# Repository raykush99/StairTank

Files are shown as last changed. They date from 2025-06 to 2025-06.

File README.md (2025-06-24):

**Stair Tank**      
Simply put, my project is a tank that can climb stairs. It is a RC car that uses treads to move instead of wheels. But to add on that, it had a special function that allows it to go up and down stairs. It also has a camera that can broadcast a live feed back to a device. The tank is controlled using the "wasd" keys on a computer.         

**Why a tank**         
I choose to build a tank since I have always wanted to make a remote control vehicle that can go anywhere. I always dreamed of being able to sit in any room and drive a car around the house, using a camera to see where it is. But I always face a boundry, since most RC cars are limited to being on one floor. Due to this, I decided to make something that can go up and down stairs, giving it almost limitless reach. From this also came the idea of being anywhere in the house, and being able to call the tank to come to your position. Or sitting in the basement and sending a box upsatirs on the car without moving muscle. This is what inspired me to make a RC car that can go anywhere, even up stairs.       
     
       
     

**BOM**      

|Item	|Unit Price|	Quantity|	Total Price|	Link|
| --- | -----|---|---|-----|
|Tank Treads	|12.8|	3|	38.4|	https://www.amazon.com/gp/product/B0BKFQPS5T/ref=ox_sc_act_title_10?smid=A3DNF7PMWIJNTG&psc=1|
|Tread Grip|	2.36	|3|	7.08	|https://www.amazon.com/gp/product/B0BHQKYL83/ref=ox_sc_act_title_1?smid=A2OG7GOMLN7OOH&th=1|
|DC Motor	|15.99	|2	|31.98|	https://www.amazon.com/gp/product/B09SZ3GC13/ref=ox_sc_act_title_9?smid=AMXT7HV26EJPE&th=1|
|Motor Driver|	6.98	|1	|6.98|	https://www.amazon.com/gp/product/B0DPPWFZ1C/ref=ox_sc_act_title_7?smid=A19I4QHRSJAHJQ&th=1|
|Servo Motor|	9.99|	1	|9.99	|https://www.amazon.com/gp/product/B09BZ5955Z/ref=ox_sc_act_title_6?smid=A19FRW2DHVT2CC&th=1|
|Battery	|15.99|	1	|15.99|	https://www.amazon.com/gp/product/B0C243MXMQ/ref=ox_sc_act_title_8?smid=A3FKMD6P089KQA&th=1|
|Switch	|5.29|	1	|5.29	|https://www.amazon.com/Rocker-Switch%EF%BC%8C6Pcs-Latching-Pre-Wired-KCD1-X-Y/dp/B07L9JWVVR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 303622651e1e&pf_rd_p=751acc83-5c05-42d0-a15e-303622651e1e&pf_rd_r=546HWN4ZDGJN150SFFDJ&pd_rd_wg=p7Kxs&pd_rd_r=c3ec9eda-920d-4ffe-a6fc-3ae20d09d0dd&pd_rd_i=B07L9JWVVR&psc=1|
|Voltage Stepdown|	8.99|	1	|8.99|	https://www.amazon.com/gp/product/B09DGDQ48H/ref=ox_sc_act_title_2?smid=A25NZ3OT6I61PQ&th=1|
|Esp32 microcontroller with camera	|14.99	|1	|14.99	|https://www.amazon.com/gp/product/B0F4DKTBR9/ref=ox_sc_act_title_5?smid=A23ZQFJGQ73FV0&th=1|
|ABS 1/8"	|35.99|	1	|35.99	|https://www.amazon.com/gp/product/B0CLVQV2RW/ref=ox_sc_act_title_4?smid=A14NQTB8LBA47J&th=1|
|ABS 0.06"	|17.99	|1	|17.99	|https://www.amazon.com/gp/product/B0B429DZ7H/ref=ox_sc_act_title_3?th=1|
|16 awg wire|	7.99|	1	|7.99	|https://www.amazon.com/Voltage-Automotive-Primary-Security-Electrical/dp/B0CZ73SQP8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|
|electrical tape|	3.59	|1|	3.59|	https://www.amazon.com/Wapodeai-Electrical-Temperature-Resistance-Waterproof/dp/B07ZWC2VLX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|
|Gyro sensor|	0	|1|	0	|own|
|Total Price		|	205.25|

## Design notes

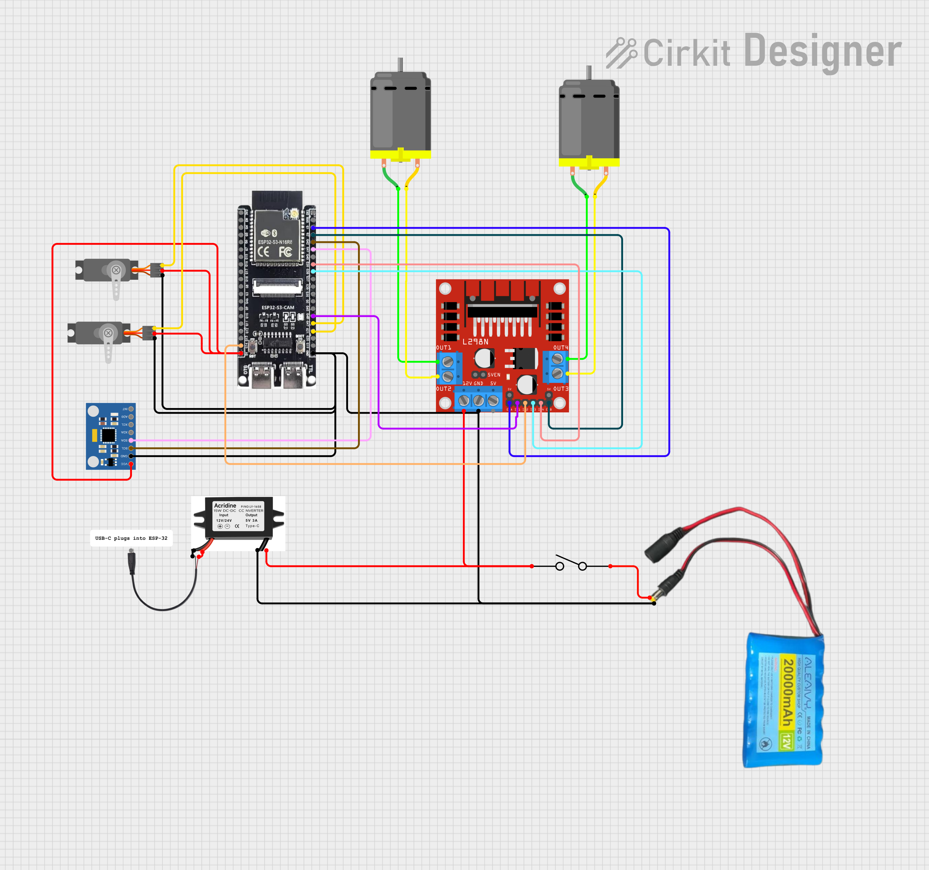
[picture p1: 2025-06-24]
circuit.png

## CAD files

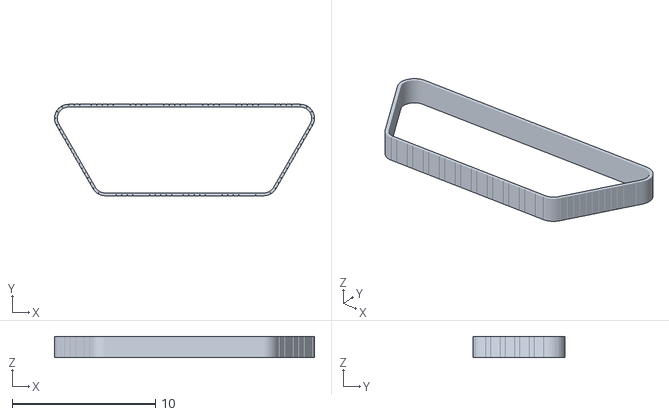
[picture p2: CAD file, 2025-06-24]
CAD/Tread Main.stl
18.2 x 6.40 x 1.50

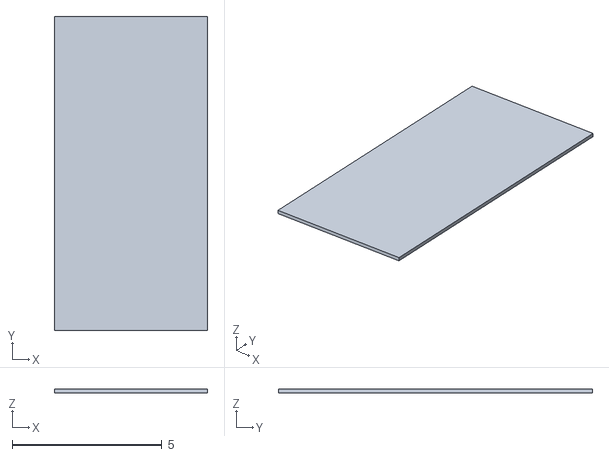
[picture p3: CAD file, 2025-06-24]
CAD/Back panel.stl
5.12 x 10.5 x 0.125

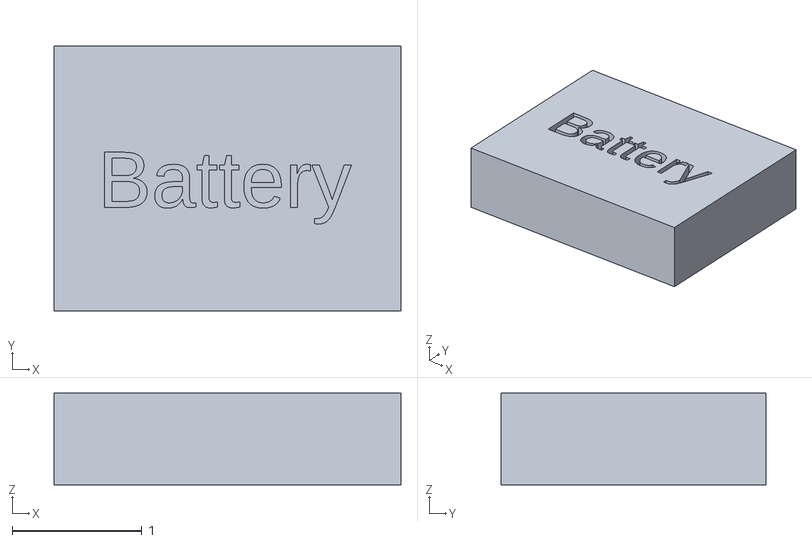
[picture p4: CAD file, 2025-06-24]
CAD/battery.stl
2.68 x 2.05 x 0.709

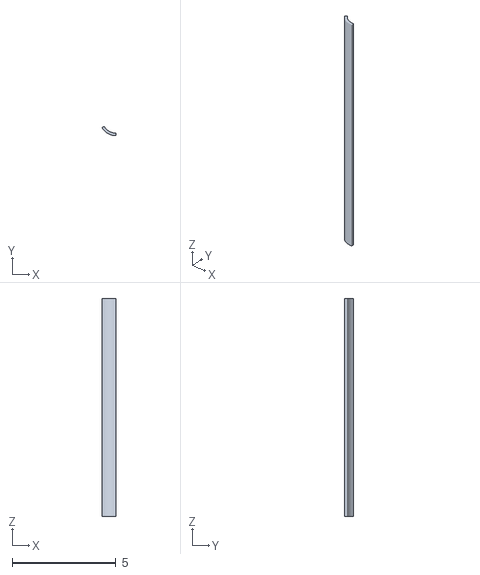
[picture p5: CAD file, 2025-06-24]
CAD/Bottom Back.stl
0.68 x 0.455 x 10.5

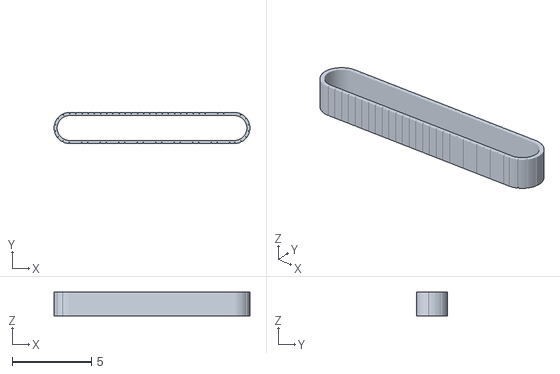
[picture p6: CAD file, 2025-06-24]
CAD/Tread Assist.stl
12.4 x 1.97 x 1.50

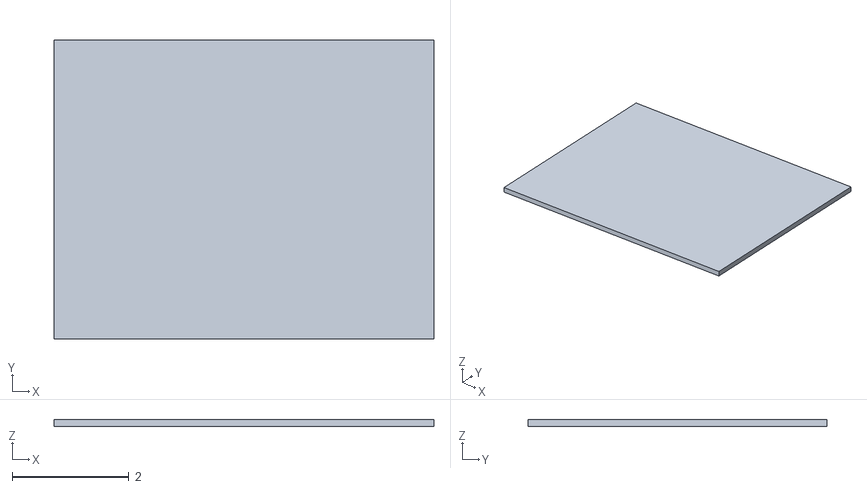
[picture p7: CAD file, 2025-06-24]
CAD/Front Panel.stl
6.50 x 5.12 x 0.125

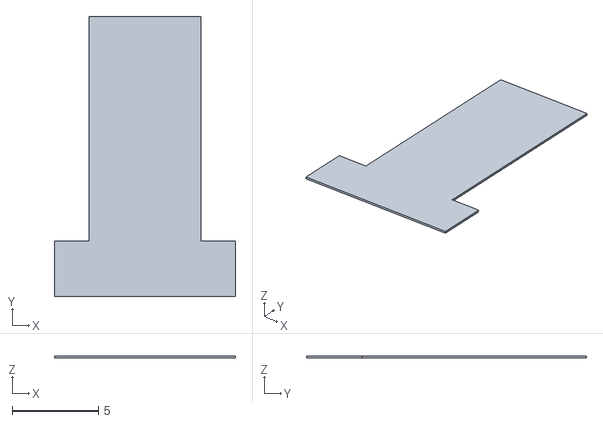
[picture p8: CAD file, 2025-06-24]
CAD/Top Panel.stl
10.5 x 16.2 x 0.125

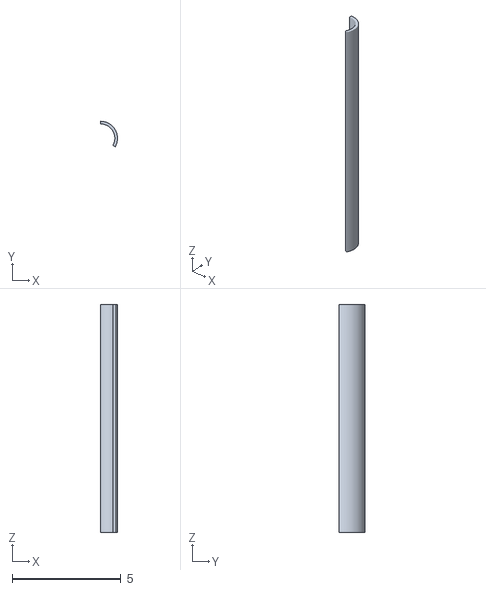
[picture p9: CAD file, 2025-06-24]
CAD/Top Back.stl
0.785 x 1.18 x 10.5

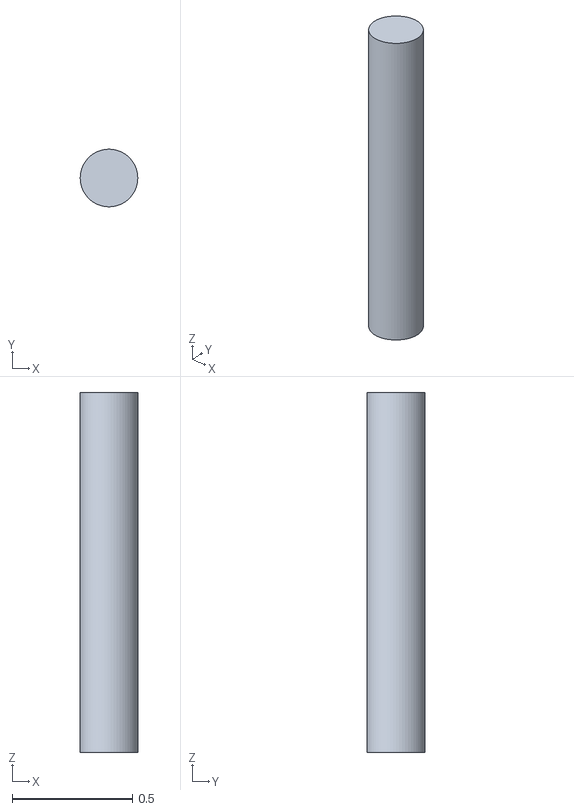
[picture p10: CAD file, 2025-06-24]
CAD/Small axle.stl
0.24 x 0.24 x 1.50

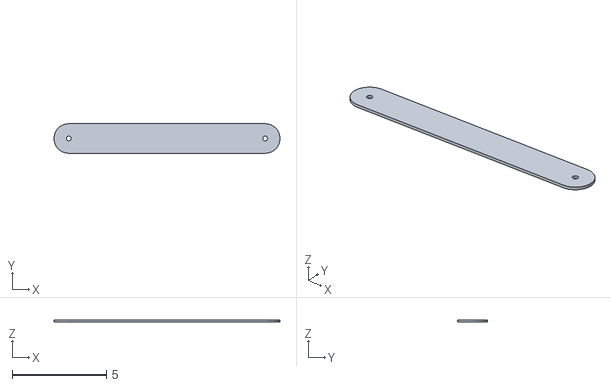
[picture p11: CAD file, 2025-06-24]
CAD/Assist Panels.stl
12.0 x 1.57 x 0.125

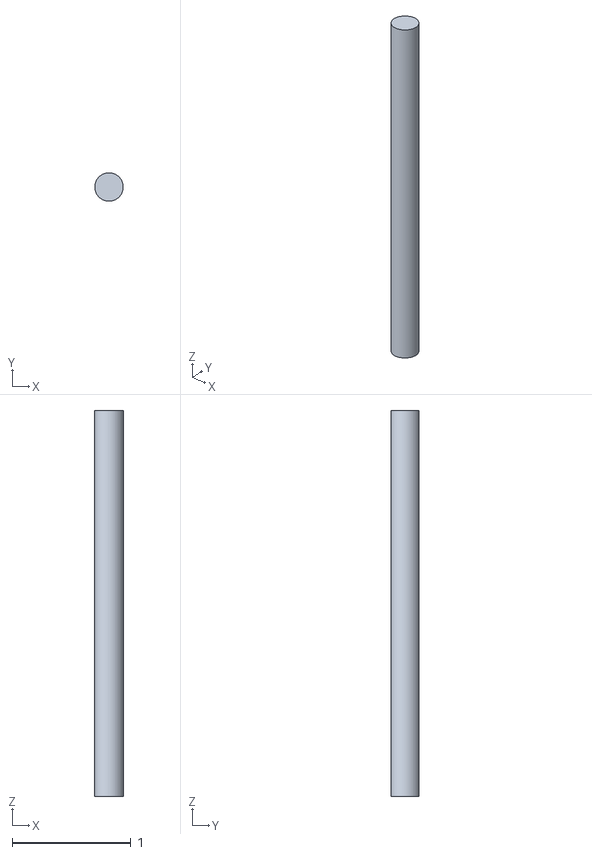
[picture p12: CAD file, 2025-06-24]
CAD/Large axle.stl
0.24 x 0.24 x 3.25

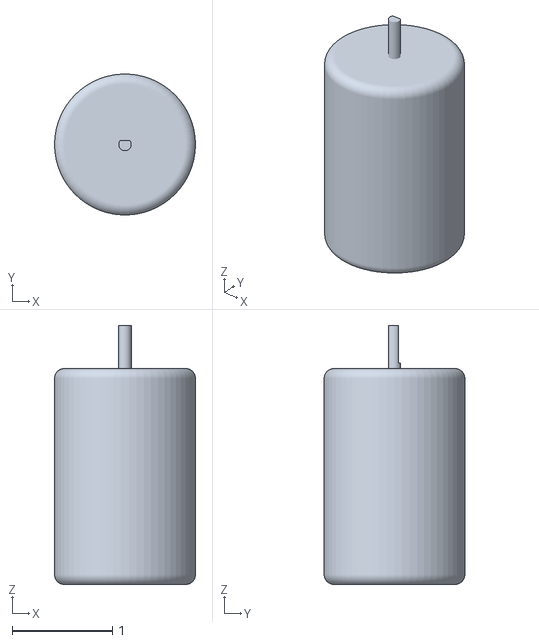
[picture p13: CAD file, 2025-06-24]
CAD/motor.stl
1.41 x 1.41 x 2.59

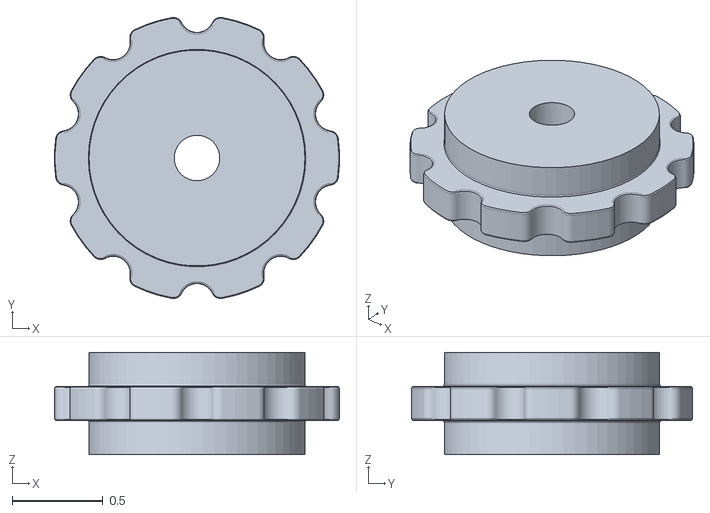
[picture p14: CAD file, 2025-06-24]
CAD/Tread Gear.stl
1.57 x 1.55 x 0.562

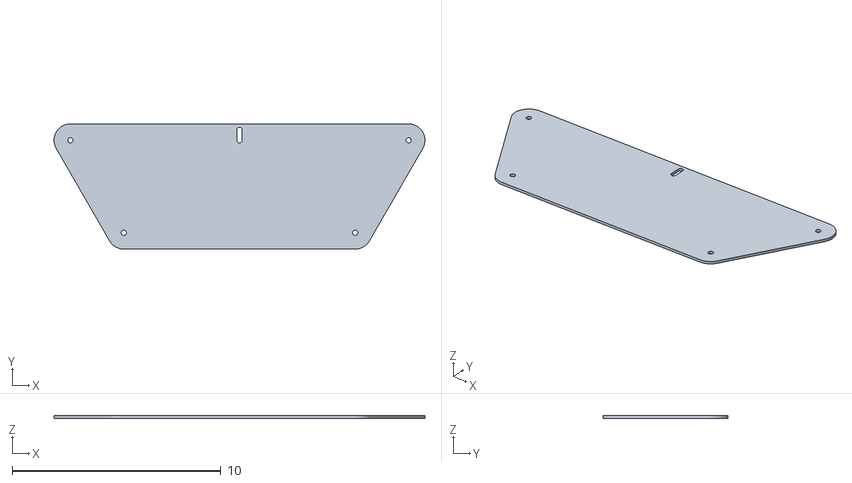
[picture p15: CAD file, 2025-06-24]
CAD/Side Walls.stl
17.8 x 6.00 x 0.125

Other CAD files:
CAD/Bottom Front.stl
CAD/Top Front.stl
CAD/Bottom Panel.stl
CAD/servo.stl

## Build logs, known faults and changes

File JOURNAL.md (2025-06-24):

---
title: "Stair Tank"
author: "Kush Ray"
description: "A tank style RC car with camera that is able to go up and down stairs"
created_at: "2025-06-14"
---
**Total time spent: 13**

**Day 1 June  13**       

Today I began my researching different methods of building a stair climbing robot. The main method I found was a modular robot in which each section could lift up one by one to climb stairs one at a time. I did not use this since I wanted to be able to place items on the top of my robot, and this would make that difficult. I wondered if there was a way the robot could directly go over the stairs, but that would require wheels bigger than 8 inches in raduis. I then had the idea of using tank treads. However, that would still need very long treads. Instead, I decided to make a way to expand the size of the treads, by including another set that can come out of the body of the robot. I used some spare LEGO pieces to make a quick prototype of the tread design, making sure it would work. After much trial and error, I found that including studs on the tracks helped it hold onto the stairs better. I also concluded that keeping a 45 degree angle was most effective in getting the treads to initially pull the robot up.    
             

**Time spent: 1.5 hours**

**Day 2 June 16**             
Today I began working on the CAD. I knew the tank had to be large to climb the stairs, so I decided to make it 18" x 12" x 12". I started making the panel that would hold the treads, and added fillets on the corners so the treads would be completly flush against the panel. I also added an extra hole in case the treads need to be tensioned. Next, I make a simple CAD of the wheel as well as making the axles. I did the same thing to make the panels for the expanding treads, and made panels to connect the two tread panels together to get a basic form of the tank. I assembled all the parts together to see how the second treads would flip out from the front. One hard part was making the curved panels since they had to be the right angle and radius to work. I managed to use the sketch of the tread panels as reference for the radius and angle to make the curves panels.            

      
      

**Time spent: 3 hours**

**Day 3 June 17**             
Today was mainly for finding the parts to build the tank. I decided to use lego treads, since they could be fit to any size, and I was able to add grip stubs on them to help climb the stairs. Doing some research, I also found that the L298N board was best for controlling the direction and speed of two motors. I also decied that a 35T motor would give the best torque and spped for the tank, and found a rechargable 12V battery to use. The last thing I thought of was how to flip the secondary treads. I decided on a servo motor since it would be best on keeping a 45 degree angle with the stairs. I also found strong servos to be able to lift the secondary treads.           

               
**Time spent: 1 hour**

**Day 4 June 19**            
Today I edited my cad to change the size based on parts I found and to add more detail. I started by adding detail to the gears. Then, I had to make the axles and space between the tread panels bigger, since the LEGO treads I found were bigger than I expected. After making this change, I had to fix my assembly, since the editing of the size caused some elements to become offset and merge. I also had to edit some dimensions of the panels to adjust for the large tread size. Finally, I added the treads to my design. This was the hardest and most time consuming part, since the treads werean irrugular shape. I wasn't able to animate the treads, but I was able to make a static design to simulate where they would go. I also added revolve mates and gear relations on the axle and gears to show how they will all move together.              

                                

**Time spent: 2.5 hours**

**Day 5 June 20**                
Today, I looked for the rest of the parts. Since I want a camera, I was planning on using the esp32-cam. However, this model does not have enough ports to be able to handle all the motors I need. After some searching, I found the esp32-S3-cam, a camera board with more gpio pins. I also spent some time seeing which gpio pins were usable and not taken up by the camera and other internal functions. Another problem I had was how to build the acutal tank. I though 3D printing, but the panels were too big. Instead, I decided to use polycarb or plastic. But since my design has curved parts, I eventually settled for ABS, since it is cheaper than polycarb, but also easier to bend into the curved shape I want. I spent time to plan out how I was going to cut each panel out, in order to have to buy the  least amount of material possible. I decided to use 1/8 inch for the main pieces, and 0.06 inch for the curved and smaller pieces.        

               
**Time spent: 1 hour**

**Day 5 June 20**               
My second work session on the 20th included me making the circuit diagram. I found a website that had many parts and allowed for an easy way to make visual diagrams. I started by importing in all the parts. I decided on not using a pcb, since most components were spread out and a pcb would be impractical. The cicurt included two servo motors, two dc motors, a motor driver, the esp32, the gyro sensor (to read the tilt of the tank on the stairs), a battery, a switch (to turn the power on and off), and a voltage stepdown. Halfway through wiring the power, I realized I didn't have a way to power the microcontroller. I wanted everything to have power using one battery, but the esp32 would fry with a 12V battery. I did research and found a voltage stepdown can convert the 12V to 5V. The model I found even had a usbc end to connect directly to the microcontroller to power it. Another problem was deciding which pins to use on the microcntroller. This is since some pins are connected to internal functions that may cause the pin not to work. I used the pin diagram given my the manufacturer and did research to identify which pins were safe. I was still short 2 pins, so decided to use the SD card pins since my project does not need an SD card. I then color coded the wires (red for power, black for GND, yellow for servos, random for motor control).             
                
**Time spent: 2 hours**

**Day 6 June 23**           
Today, I decided to add my motors and batteries into the CAD. Originally, I tried to find models of the motors I could upload, but I wasn't able to find any. Instead, I decided to use the scematics given to make my own simple model of the servos, DC motors, and battery. After desgining each piece, I added it to the master assembly to see if it would fit. The DC motor and servo barely overlap with a few curved pieces, but this is fine since I can slightly change the curvature of the ABS while making it to fit the motors. I also added a simple mount for the servo to rest on and a piece to attach the servo shaft to the secondard tread piece. Finnally, I decided to customize the colors of each piece to what it would look like with the real materials, letting me finally finish the CAD for the stair tank.             


       
**Time spent: 2 hours**

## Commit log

2025-06-24 Update and rename Stair Tank BOM - Sheet1.csv to BOM
2025-06-24 Update and rename BOM to BOM.csv
    [BOM.csv]
2025-06-24 Create CAD link
